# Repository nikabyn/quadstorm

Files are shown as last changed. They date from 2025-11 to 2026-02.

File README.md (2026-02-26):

# Project quadstorm (C010 Principles of Mobile Robotics)

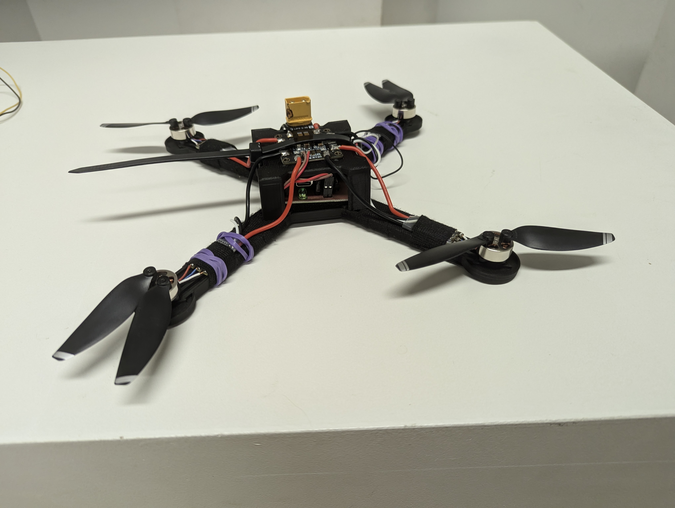
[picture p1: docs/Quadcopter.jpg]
Hier könnte ihre Werbung stehen


## Architecture
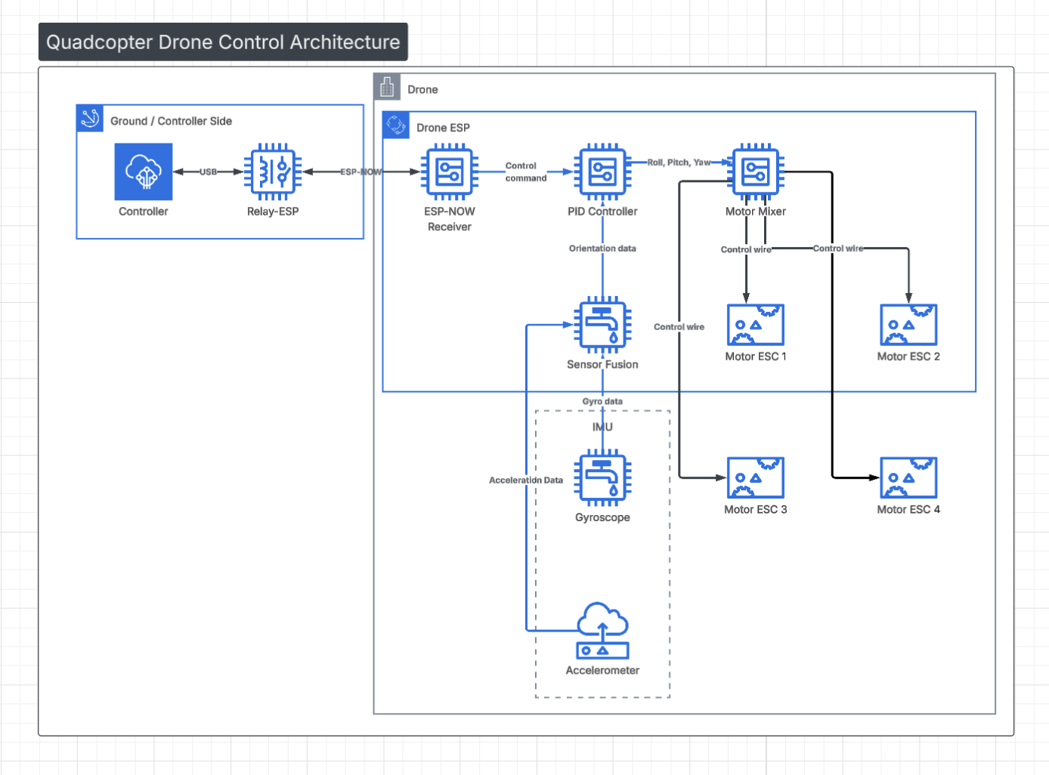
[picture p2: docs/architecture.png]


## Mainboard

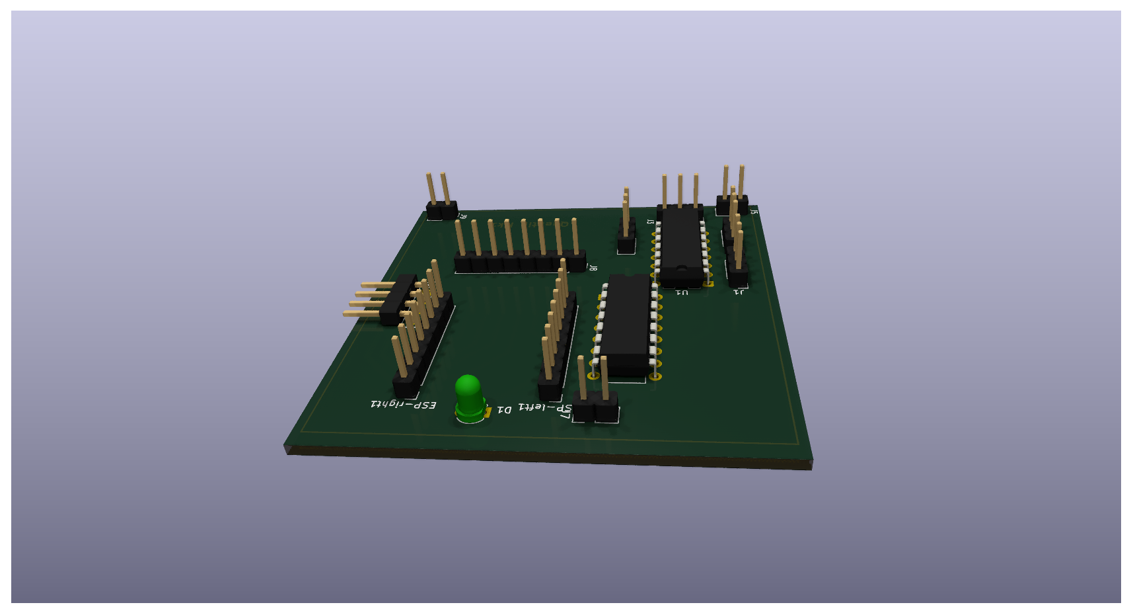
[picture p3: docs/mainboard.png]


## Parts-List:
- [BT2.0 550mAh 1S Battery](https://betafpv.com/products/bt2-0-550mah-1s-battery-4pcs#:~:text=Weight:%2013.99g/pc,VS%20450mAh%20Battery)
- IMU [BMI323](https://www.bosch-sensortec.com/products/motion-sensors/imus/bmi323/)
- Motors: [4x 2S Bldc 1503](https://www.amazon.de/dp/B0CK2KT3R3)
- ESP32-C6 ([ESP32-C6 Supermini](https://wiki.raudys.com/doku.php?id=esp32:esp32-c6_super_mini_board) / [DFR1117](https://wiki.dfrobot.com/SKU_DFR1117_Beetle_ESP32_C6))
- 74LS04 (Hex-Inverter), 74LS138 3-to-8 demux)
- [FVT LittleBee ESC 20A 2-4S](https://de.aliexpress.com/item/1005010298051292.html)
- Generic DJI compatible props
- 3d Printed Frame
- Custom Mainboard (manufactured via CNC Router)
- 12 M2x8 Screws

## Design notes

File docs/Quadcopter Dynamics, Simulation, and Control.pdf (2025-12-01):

## Quadcopter Dynamics, Simulation, and Control

## Introduction

A helicopter is a flying vehicle which uses rapidly spinning rotors to push air downwards, thus creating a thrust force keeping the helicopter aloft. Conventional helicopters have two rotors. These can be arranged as two coplanar rotors both providing upwards thrust, but spinning in opposite directions (in order to balance the torques exerted upon the body of the helicopter). The two rotors can also be arranged with one main rotor providing thrust and a smaller side rotor oriented laterally and counteracting the torque produced by the main rotor. However, these configurations require complicated machinery to control the direction of motion; a swashplate is used to change the angle of attack on the main rotors. In order to produce a torque the angle of attack is modulated by the location of each rotor in each stroke, such that more thrust is produced on one side of the rotor plane than the other. The complicated design of the rotor and swashplate mechanism presents some problems, increasing construction costs and design complexity.
A quadrotor helicopter (quadcopter) is a helicopter which has four equally spaced rotors, usually arranged at the corners of a square body. With four independent rotors, the need for a swashplate mechanism is alleviated. The swashplate mechanism was needed to allow the helicopter to utilize more degrees of freedom, but the same level of control can be obtained by adding two more rotors.
The development of quadcopters has stalled until very recently, because controlling four independent rotors has proven to be incredibly difficult and impossible without electronic assistance. The decreasing cost of modern microprocessors has made electronic and even completely autonomous control of quadcopters feasible for commercial, military, and even hobbyist purposes.
Quadcopter control is a fundamentally difficult and interesting problem. With six degrees of freedom (three translational and three rotational) and only four independent inputs (rotor speeds), quadcopters are severely underactuated. In order to achieve six degrees of freedom, rotational and translational motion are coupled. The resulting dynamics are highly nonlinear, especially after accounting for the complicated aerodynamic effects. Finally, unlike ground vehicles, helicopters have very little friction to prevent their motion, so they must provide their own damping in order to stop moving and remain stable. Together, these factors create a very interesting control problem. We will present a very simplified model of quadcopter dynamics and design controllers for our dynamics to follow a designated trajectory. We will then test our controllers with a numerical simulation of a quadcopter in flight.

## Quadcopter Dynamics

We will start deriving quadcopter dynamics by introducing the two frames in which will operate. The inertial frame is defined by the ground, with gravity pointing in the negative z direction. The body frame is defined by the orientation of the quadcopter, with the rotor axes pointing in the positive z direction and the arms pointing in the x and y directions.

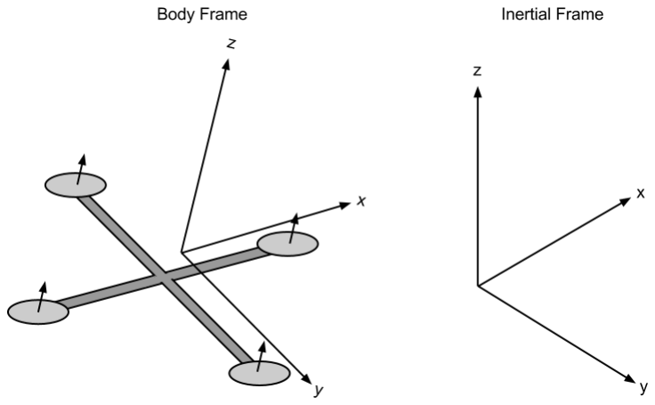
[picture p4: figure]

Quadcopter Body Frame and Inertial Frame

Kinematics

Before delving into the physics of quadcopter motion, let us formalize the kinematics in the body and inertial frames. We define the position and velocity of the quadcopter in the inertial frame as x = (x, y, z)

T and x˙ = (x˙, y˙, z˙)

T
, respectively. Similarly, we define the roll, pitch, and yaw angles in the body frame as θ = (φ, θ, ψ)

T
, with corresponding angular velocities equal to ˙θ = (φ˙,

˙θ, ψ˙)
T

. However, note that the angular velocity vector ω 6= ˙θ. The angular velocity is a vector pointing along the axis of rotation, while ˙θ is just the time derivative of yaw, pitch, and roll. In order to convert these angular velocities into the angular velocity vector, we can use the following relation:

ω =

1 | 0 | −sθ
0 | cφ | cθ

sφ
0 −sφ cθ cφ
- ˙θ

where ω is the angular velocity vector in the body frame.
We can relate the body and inertial frame by a rotation matrix R which goes from the body frame to the inertial frame. This matrix is derived by using the ZYZ Euler angle conventions and successively “undoing” the yaw, pitch, and roll.

R =

cφcψ − cθ

sφsψ | −cψsφ − cφcθ
sψ | sθ

sψ
cθ cψsφ + cφsψ | cφcθ cψ − sφsψ | −cψsθ
sφsθ | cφsθ | cθ

For a given vector ~v in the body frame, the corresponding vector is given by R~v in the inertial frame.

Physics

In order to properly model the dynamics of the system, we need an understanding of the physical properties that govern it. We will begin with a description of the motors being used for our quadcopter, and then use energy considerations to derive the forces and thrusts that these motors produce on the entire quadcopter. All motors on the quadcopter are identical, so we can analyze a single one without loss of generality. Note that adjacent propellers, however, are oriented opposite each other; if a propeller is spinning “clockwise”, then the two adjacent ones will be spinning “counter-clockwise”, so that torques are balanced if all propellers are spinning at the same rate.

Motors

Brushless motors are used for all quadcopter applications. For our electric motors, the torque produced is given by
τ = Kt(I − I0)

where τ is the motor torque, I is the input current, I0 is the current when there is no load on the motor, and Kt

is the torque proportionality constant. The voltage across the motor is the sum of the back-EMF and some resistive loss:

V = IRm + Kvω

where V is the voltage drop across the motor, Rm is the motor resistance, ω is the angular velocity of the motor, and Kv is a proportionality constant (indicating back-EMF generated per RPM). We can use this description of our motor to calculate the power it consumes. The power is

P = IV =

(τ + KtI0)(KtI0Rm + τRm + KtKvω)
Kt

2

For the purposes of our simple model, we will assume a negligible motor resistance. Then, the power becomes proportional to the angular velocity:

P ≈

(τ + KtI0)Kvω
Kt

Further simplifying our model, we assume that KtI0 τ. This is not altogether unreasonable, since I0 is the current when there is no load, and is thus rather small. In practice, this approximation holds well enough. Thus, we obtain our final, simplified equation for power:

P ≈

Kv
Kt

τω.

Forces

The power is used to keep the quadcopter aloft. By conservation of energy, we know that the energy the motor expends in a given time period is equal to the force generated on the propeller times the distance that the air it displaces moves (P · d t = F · d x). Equivalently, the power is equal to the thrust times the air velocity (P = F

d x
d t

).

P = Tvh

We assume vehicle speeds are low, so vh

is the air velocity when hovering. We also assume that the free stream velocity, v∞, is zero (the air in the surrounding environment is stationary relative to the quadcopter). Momentum theory gives us the equation for hover velocity as a function of thrust,

vh =

s
T
2ρA

where ρ is the density of the surrounding air and A is the area swept out by the rotor. Using our simplified equation for power, we can then write

P =

Kv
Kt

τω =

KvKτ
Kt

Tω =

T

3
2
p
2ρA

Note that in the general case, τ =~r × ~F; in this case, the torque is proportional to the thrust T by some constant ratio Kτ determined by the blade configuration and parameters. Solving for the thrust magnitude T, we obtain that thrust is proportional to the square of angular velocity of the motor:

T =

KvKτ

p
2ρA
Kt

ω

!2
= kω

2

where k is some appropriately dimensioned constant. Summing over all the motors, we find that the total thrust on the quadcopter (in the body frame) is given by

TB =

4
∑

i=1

Ti = k

0
0
∑ ωi

2

In addition to the thrust force, we will model friction as a force proportional to the linear velocity in each direction. This is a highly simplified view of fluid friction, but will be sufficient for our modeling and simulation. Our global drag forces will be modeled by an additional force term

FD =

−kdx˙
−kdy˙
−kdz˙

If additional precision is desired, the constant kd can be separated into three separate friction constants, one for each direction of motion. If we were to do this, we would want to model friction in the body frame rather than the inertial frame.

Torques

Now that we have computed the forces on the quadcopter, we would also like to compute the torques. Each rotor contributes some torque about the body z axis. This torque is the torque required to keep the propeller spinning and providing thrust; it creates the instantaneous angular acceleration and overcomes the frictional drag forces. The drag equation from fluid dynamics gives us the frictional force:

FD =

1
2

ρCD Av²

where ρ is the surrounding fluid density, A is the reference area (propeller cross-section, not area swept out by the propeller), and CD is a dimensionless constant. This, while only accurate in some in some cases, is good enough for our purposes. This implies that the torque due to drag is given by

τD =

1
2

RρCD Av² =

1
2

RρCD A(ωR)

2 = bω

2

where ω is the angular velocity of the propeller, R is the radius of the propeller, and b is some appropriately dimensioned constant. Note that we’ve assumed that all the force is applied at the tip of the propeller, which is certainly inaccurate; however, the only result that matters for our purposes is that the drag torque is proportional to the square of the angular velocity. We can then write the complete torque about the z axis for the ith motor:

τz = bω

2 + IMω˙

where IM is the moment of inertia about the motor z axis, ω˙ is the angular acceleration of the propeller, and b is our drag coefficient. Note that in steady state flight (i.e. not takeoff or landing), ω˙ ≈ 0, since most of the time the propellers will be maintaining a constant (or almost constant) thrust and won’t be accelerating. Thus, we ignore this term, simplifying the entire expression to
τz = (−1)

i+1
bωi

2
where the (−1)

i+1
term is positive for the ith propeller if the propeller is spinning clockwise and negative if it is spinning counterclockwise. The total torque about the z axis is given by the sum of all the torques from each propeller:

τψ = b

ω1

2 − ω2

2 + ω3

2 − ω4

2

The roll and pitch torques are derived from standard mechanics. We can arbitrarily choose the i = 1 and i = 3 motors to be on the roll axis, so

τφ = ∑r × T = L(kω1
2 − kω3
) = Lk(ω1

2 − ω3
)

Correspondingly, the pitch torque is given by a similar expression

τθ = Lk(ω2

2 − ω4

2
)

where L is the distance from the center of the quadcopter to any of the propellers. All together, we find that the torques in the body frame are

τB =

Lk(ω1

2 − ω3
2
)
Lk(ω2

2 − ω4

2
)
b
ω1

2 − ω2
2 + ω3
2 − ω4

2

The model we’ve derived so far is highly simplified. We ignore a multitude of advanced effects that contribute to the highly nonlinear dynamics of a quadcopter. We ignore rotational drag forces (our rotational velocities are relatively low), blade flapping (deformation of propeller blades due to high velocities and flexible materials), surrounding fluid velocities (wind), etc. With that said, we now have all the parts necessary to write out the dynamics of our quadcopter.

Equations of Motion

In the inertial frame, the acceleration of the quadcopter is due to thrust, gravity, and linear friction. We can obtain the thrust vector in the inertial frame by using our rotation matrix R to map the thrust vector from the body frame to the inertial frame. Thus, the linear motion can be summarized as

mx¨ =

0
0
−mg
- + RTB + FD

where ~x is the position of the quadcopter, g is the acceleration due to gravity, FD is the drag force, and TB is the thrust vector in the body frame.
While it is convenient to have the linear equations of motion in the inertial frame, the rotational equations of motion are useful to us in the body frame, so that we can express rotations about the center of the quadcopter instead of about our inertial center. We derive the rotational equations of motion from Euler’s equations for rigid body dynamics. Expressed in vector form, Euler’s equations are written as

Iω˙ + ω × (Iω) = τ

where ω is the angular velocity vector, I is the inertia matrix, and τ is a vector of external torques. We can rewrite this as

ω˙ =

ω˙ x
ω˙ y
ω˙ z
- = I

−1
(τ − ω × (Iω)).

We can model our quadcopter as two thin uniform rods crossed at the origin with a point mass (motor) at the end of each. With this in mind, it’s clear that the symmetries result in a diagonal inertia matrix of the form

I =

Ixx | 0 | 0
0 | Iyy | 0
0 | 0 | Izz

Therefore, we obtain our final result for the body frame rotational equations of motion

ω˙ =

τφ Ixx

−1

τθ

Iyy

−1

τψIzz

−1

- −

Iyy−Izz
Ixx

ωyωz
Izz−Ixx
Iyy

ωxωz
Ixx−Iyy
Izz

ωxωy

## Simulation

Now that we have complete equations of motion describing the dynamics of the system, we can create a simulation environment in which to test and view the results of various inputs and controllers. Although more advanced methods are available, we can quickly write a simulator which utilizes Euler’s method for solving differential equations to evolve the system state. In MATLAB, this simulator would be written as follows.

1 | % Simulation times, in seconds.
2 | start_time = 0;
3 | end_time = 10;
4 | dt = 0.005;
5 | times = start_time:dt:end_time;

6
7 | % Number of points in the simulation.
8 | N = numel(times);

9
10 | % Initial simulation state.
11 | x = [0; 0; 10];
12 | xdot = zeros(3, 1);
13 | theta = zeros(3, 1);

14
15 | % Simulate some disturbance in the angular velocity.
16 | % The magnitude of the deviation is in radians / second.
17 | deviation = 100;
18 | thetadot = deg2rad(2 * deviation * rand(3, 1) - deviation);

19
20 | % Step through the simulation, updating the state.
21 | for t = times
22 | % Take input from our controller.
23 | i = input(t);

24
25 | omega = thetadot2omega(thetadot, theta);

26
27 | % Compute linear and angular accelerations.
28 | a = acceleration(i, theta, xdot, m, g, k, kd);
29 | omegadot = angular_acceleration(i, omega, I, L, b, k);

30
31 | omega = omega + dt * omegadot;
32 | thetadot = omega2thetadot(omega, theta);
33 | theta = theta + dt * thetadot;
34 | xdot = xdot + dt * a;
35 | x = x + dt * xdot;
36 | end

We would then need functions to compute all of the physical forces and torques.

1 | % Compute thrust given current inputs and thrust coefficient.
2 | function T = thrust(inputs, k)
3 | % Inputs are values for ωi
| 2
4 | T = [0; 0; k * sum(inputs)];
5 | end

6
7 | % Compute torques, given current inputs, length, drag coefficient, and thrust coefficient.
8 | function tau = torques(inputs, L, b, k)
9 | % Inputs are values for ωi
| 2
10 | tau = [
11 | L * k * (inputs(1) - inputs(3))

L * k * (inputs(2) - inputs(4))
b * (inputs(1) - inputs(2) + inputs(3) - inputs(4))

];
end

function a = acceleration(inputs, angles, xdot, m, g, k, kd) gravity = [0; 0; -g];
R = rotation(angles);
T = R * thrust(inputs, k);
Fd = -kd * xdot;
a = gravity + 1 / m * T + Fd;
end

function omegadot = angular_acceleration(inputs, omega, I, L, b, k) tau = torques(inputs, L, b, k);
omegaddot = inv(I) * (tau - cross(omega, I * omega));
end

We would also need values for all of our physical constants, a function to compute the rotation matrix R, and functions to convert from an angular velocity vector ω to the derivatives of roll, pitch, and yaw and vice-versa. These are not shown. We can then draw the quadcopter in a three-dimensional visualization which is updated as the simulation is running.

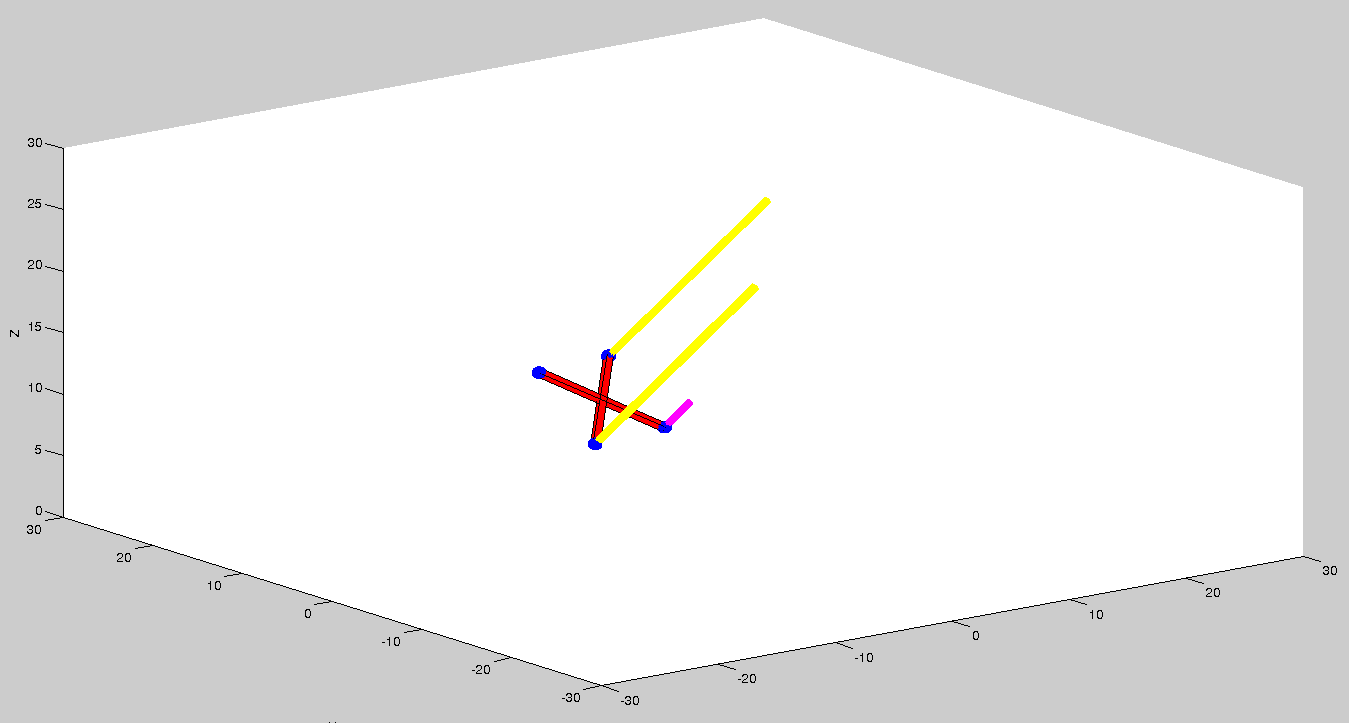
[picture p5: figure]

Quadcopter Simulation. Bars above each propeller represent, roughly, relative thrust magnitudes.

## Control

The purpose of deriving a mathematical model of a quadcopter is to assist in developing controllers for physical quadcopters. The inputs to our system consist of the angular velocities of each rotor, since all we can control is the voltages across the motors. Note that in our simplified model, we only use the square of the angular velocities, ωi

2
, and never the angular
velocity itself, ωi
. For notational simplicity, let us introduce the inputs γi = ωi

2
. Since we
can set ωi

, we can clearly set γi as well. With this, we can write our system as a first order differential equation in state space. Let x1 be the position in space of the quadcopter, x2 be the quadcopter linear velocity, x3 be the roll, pitch, and yaw angles, and x4 be the angular velocity vector. (Note that all of these are 3-vectors.) With these being our state, we can write the state space equations for the evolution of our state.

x˙1 = x2

x˙2 =

0
0
−g
- +

1
m

RTB +

1
m

FD

x˙3 =

1 | 0 | −sθ
0 | cφ | cθ sφ
0 −sφ | cθ cφ

−1
x4

x˙4 =

τφ Ixx

−1

τθ

Iyy

−1

τψIzz

−1

- −

Iyy−Izz
Ixx

ωyωz
Izz−Ixx
Iyy

ωxωz
Ixx−Iyy
Izz

ωxωy

Note that our inputs are not used in these equations directly. However, as we will see, we can choose values for τ and T, and then solve for values of γi

PD Control

In order to control the quadcopter, we will use a PD control, with a component proportional to the error between our desired trajectory and the observed trajectory, and a component proportional to the derivative of the error. Our quadcopter will only have a gyro, so we will only be able to use the angle derivatives φ˙,

˙θ, and ψ˙ in our controller; these measured values will give us the derivative of our error, and their integral will provide us with the actual error. We would like to stabilize the helicopter in a horizontal position, so our desired velocities and angles will all be zero. Torques are related to our angular velocities by τ = I

¨θ, so we would
like to set the torques proportional to the output of our controller, with τ = Iu(t). Thus,

τφ
τθ
τψ
- =

−Ixx
Kdφ˙ + Kp

R T
0

φ˙d t

−Iyy
Kd

˙θ + Kp

R T
0

˙θd t

−Izz
Kdψ˙ + Kp

R T
0

ψ˙d t

We have previously derived the relationship between torque and our inputs, so we know that

τB =

Lk(γ1 − γ3)
Lk(γ2 − γ4)
b (γ1 − γ2 + γ3 − γ4)
- =

−Ixx
Kdφ˙ + Kp

R T
0

φ˙d t

−Iyy
Kd

˙θ + Kp

R T
0

˙θd t

−Izz
Kdψ˙ + Kp

R T
0

ψ˙d t

This gives us a set of three equations with four unknowns. We can constrain this by enforcing the constraint that our inputs must keep the quadcopter aloft:

T = mg.

Note that this equation ignores the fact that the thrust will not be pointed directly up. This will limit the applicability of our controller, but should not cause major problems for small deviations from stability. If we had a way of determining the current angle accurately, we could compensate. If our gyro is precise enough, we can integrate the values obtained from the gyro to get the angles θ and φ. In this case, we can calculate the thrust necessary to keep the quadcopter aloft by projecting the thrust mg onto the inertial z axis. We find that

Tproj = mg cos θ cos φ

Therefore, with a precise angle measurement, we can instead enforce the requirement that the thrust be equal to
T =

mg
cos θ cos φ in which case the component of the thrust pointing along the positive z axis will be equal to mg. We know that the thrust is proportional to a weighted sum of the inputs:

T =

mg
cos θ cos φ

= k∑γi =⇒ ∑γi =

mg
k cos θ cos φ

With this extra constraint, we have a set of four linear equations with four unknowns γi . We
can then solve for each γi

, and obtain the following input values:

γ1 =

mg
4k cos θ cos φ

−

2beφ Ixx + eψIzzkL
4bkL

γ2 =

mg
4k cos θ cos φ

+

eψIzz
4b

−

eθ

Iyy
2kL

γ3 =

mg
4k cos θ cos φ

−

−2beφ Ixx + eψIzzkL
4bkL

γ4 =

mg
4k cos θ cos φ

+

eψIzz
4b

+

eθ

Iyy
2kL

This is a complete specification for our PD controller. We can simulate this controller using our simulation environment. The controller drives the angular velocities and angles to zero.

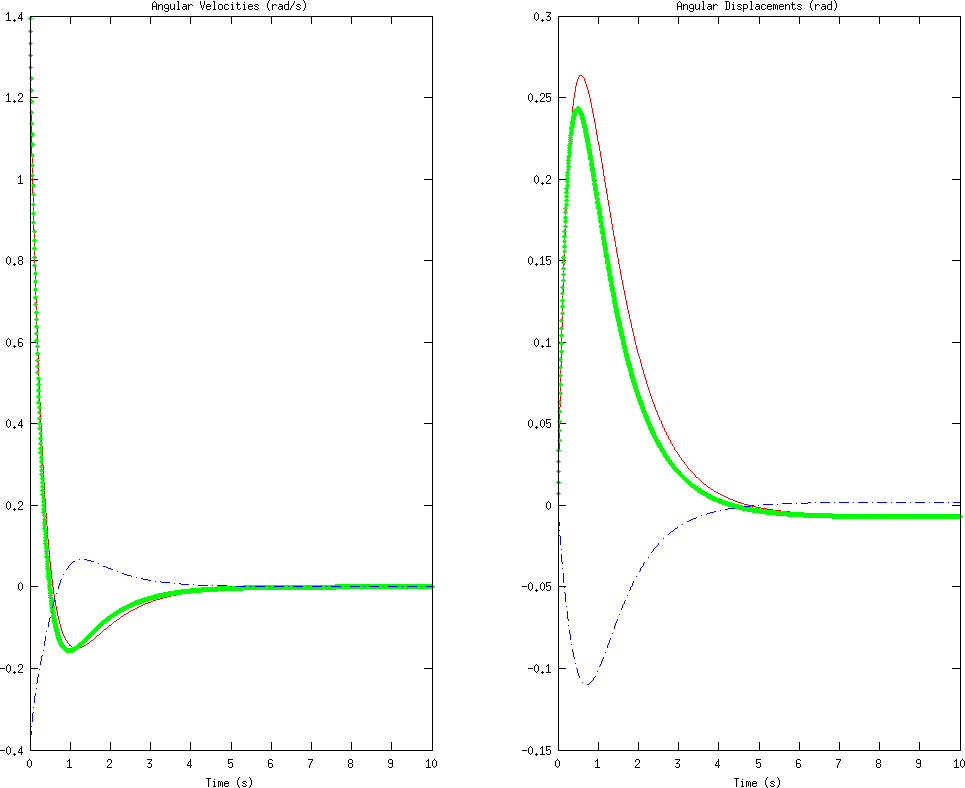
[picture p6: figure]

Left: Angular velocities. Right: angular displacements. φ, θ, ψ are coded as red, green, and blue.

However, note that the angles are not completely driven to zero. The average steady state error (error after 10 seconds of simulation) is approximately 0.3◦
. This is a common problem with using PD controllers for mechanical systems, and can be partially alleviated with a PID controller, as we will discuss in the next section.
In addition, note that since we are only controlling angular velocities, our positions and linear velocities do not converge to zero. However, the z position will remain constant, because we have constrained the total vertical thrust to be such that it keeps the quadcopter perfectly aloft, without ascending or descending. However, this is really nothing more than a curiosity. With the limited sensing that we have available to us, there is nothing we can do to control the linear position and velocity of the quadcopter. While in theory we could compute the linear velocities and positions from the angular velocities, in practice the values will be so noisy as to be completely useless. Thus, we will restrict ourselves to just stabilizing the quadcopter angle and angular velocity. (Traditionally, navigation is done by a human, and stabilization is there simply to make control easier for the human operator.)

We have implemented this PD control for use in our simulation. The controller is implemented as a function which is given some state (corresponding to controller state, not system state) and the sensor inputs, and must compute the inputs γi and the updated state. The code for a PD control follows.

% Compute system inputs and updated state.
% Note that input = [γ1, . . ., γ4]
function [input, state] = pd_controller(state, thetadot) % Controller gains, tuned by hand and intuition.
Kd = 4;
Kp = 3;

% Initialize the integral if necessary. if ˜isfield(state, ’integral’) params.integral = zeros(3, 1);
end

% Compute total thrust
total = state.m * state.g / state.k / (cos(state.integral(1)) * cos(state.integral(2)));

% Compute errors
e = Kd * thetadot + Kp * params.integral;

% Solve for the inputs, γi
input = error2inputs(params, accels, total);

% Update the state
params.integral = params.integral + params.dt .* thetadot; end

PID Control

PD controllers are nice in their simplicity and ease of implementation, but they are often inadequate for controlling mechanical systems. Especially in the presence of noise and disturbances, PD controllers will often lead to steady state error. A PID control is a PD control with another term added, which is proportional to the integral of the process variable. Adding an integral term causes any remaining steady-state error to build up and enact a change, so a PID controller should be able to track our trajectory (and stabilize the quadcopter) with a significantly smaller steady-state error. The equations remain identical to the ones presented in the PD case, but with an additional term in the error:

eφ = Kdφ˙ + Kp

Z T

0

φ˙d t + Ki

Z T

0

Z T

0

φ˙d td t

eθ = Kd

˙θ + Kp

Z T

0

˙θd t + Ki

Z T

0

Z T

0

˙θd td t

eψ = Kdψ˙ + Kp

Z T

0

ψ˙d t + Ki

Z T

0

Z T

0

ψ˙d td t

However, PID controls come with their own shortcomings. One problem that commonly occurs with a PID control is known as integral windup.

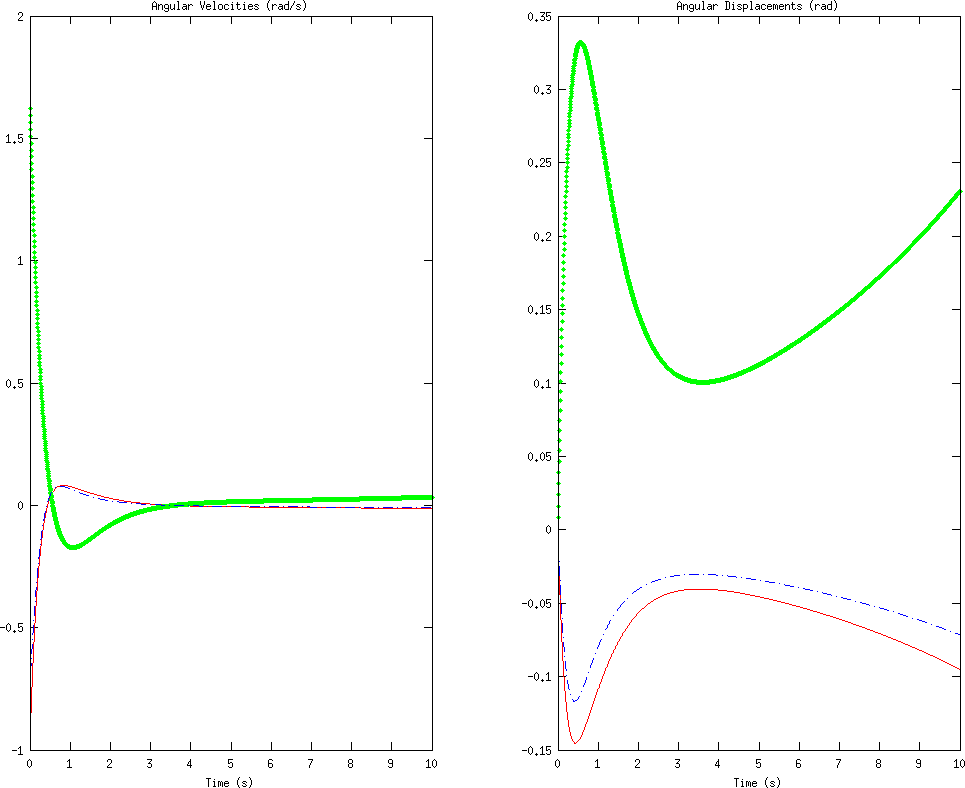
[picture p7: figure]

In some cases, integral wind-up can cause lengthy oscillations instead of settling. In other cases, wind-up may actually cause the system to become unstable, instead of taking longer to reach a steady state.

If there is a large disturbance in the process variable, this large disturbance is integrated over time, becoming a still larger control signal (due to the integral term). However, even once the system stabilizes, the integral is still large, thus causing the controller to overshoot its target. It may then begin a series of dieing down oscillations, become unstable, or simply take an incredibly long time to reach a steady state. In order to avoid this, we disable the integral function until we reach something close to the steady state. Once we are in a controllable region near the desired steady state, we turn on the integral function, which pushes the system towards a low steady-state error.

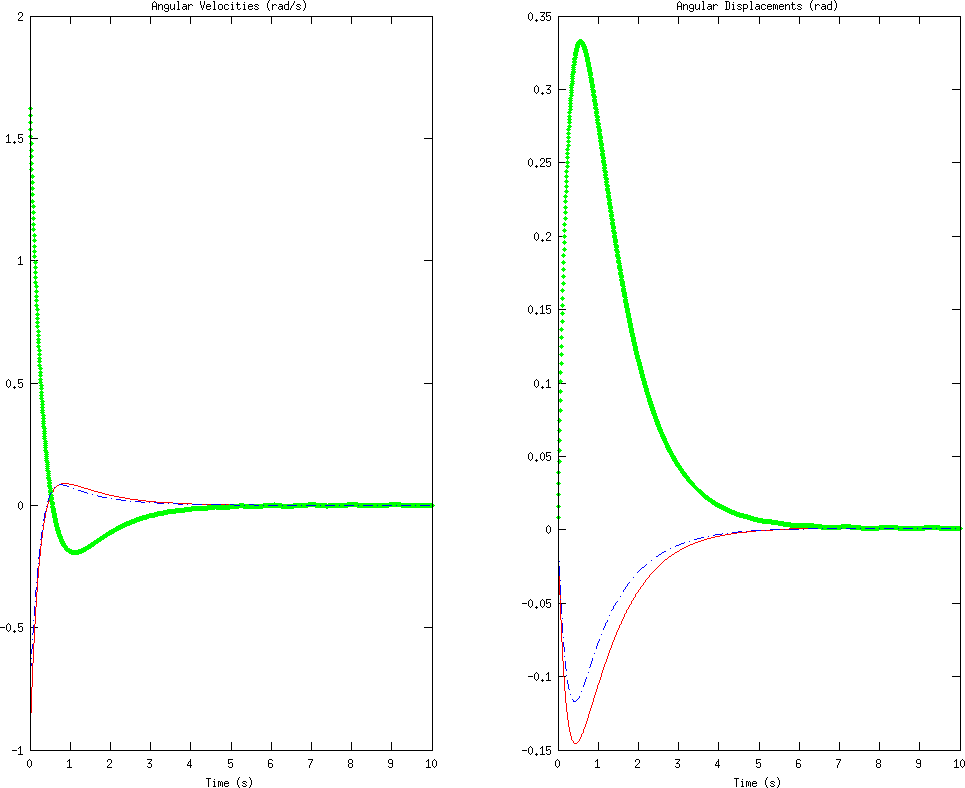
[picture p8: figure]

With a properly implemented PID, we achieve an error of approximately 0.06◦ after 10 seconds.
We have implemented this PID control for use in simulation, in the same way as with the PD controller shown earlier. Note that there is an additional parameter to tune in a PID. The disturbances used for all the test cases are identical, shown to compare the controllers.

% Compute system inputs and updated state.
% Note that input = [γ1, . . ., γ4]
function [input, state] = pid_controller(state, thetadot) % Controller gains, tuned by hand and intuition.
Kd = 4;
Kp = 3;
Ki = 5.5;

% Initialize the integral if necessary. if ˜isfield(state, ’integral’) params.integral = zeros(3, 1); params.integral2 = zeros(3, 1); end

% Prevent wind-up
if max(abs(params.integral2)) > 0.01 params.integral2(:) = 0;
end

% Compute total thrust
total = state.m * state.g / state.k / (cos(state.integral(1)) * cos(state.integral(2)));

% Compute errors

24 | e = Kd * thetadot + Kp * params.integral - Ki * params.integral2;
26 | % Solve for the inputs, γi
27 | input = error2inputs(params, accels, total);

28
29 | % Update the state
30 | params.integral = params.integral + params.dt .* thetadot;
31 | params.integral2 = params.integral2 + params.dt .* params.integral;
32 | end

Automatic PID Tuning

Although PID control has the potential to perform very well, it turns out that the quality of the controller is highly dependent on the gain parameters. Tuning the parameters by hand may be quite difficult, as the ratios of the parameters is as important as the magnitudes of the parameters themselves; often, tuning parameters requires detailed knowledge of the system and an understanding of the conditions in which the PID control will be used. The parameters we chose previously were tuned by hand for good performance, simply by running simulations with many possibly disturbances and parameter values, and choosing something that worked reasonably well. This method is clearly suboptimal, not only because it can be very difficult and labor-intensive (and sometimes more or less impossible) but also because the resulting gains are not in any way guaranteed to be optimal or even close to optimal.
Ideally, we would be able to use an algorithm to analyze a system and output the “optimal” PID gains, for some reasonable definition of optimal. This problem has been studied in depth, and many methods have been proposed. Many of these methods require detailed knowledge of the system being modeled, and some rely on properties of the system, such as stability or linearity. The method we will use for choosing our PID parameters is a method known as extremum seeking.
Extremum seeking works exactly as the name implies. We define the “optimal” set of parameters as some vector ~θ = (Kp, Ki
, Kd

) which minimizes some cost function J(~θ). In our case, we would like to define a cost function that penalizes high error and error over extended durations of time. One candidate cost function is given by

J(~θ) = 1 tf − to

# Z tf

t0

e(t,~θ)
2d t

where e(t,~θ) is the error in following some reference trajectory with some initial disturbance using a set of parameters ~θ. Suppose we were able to somehow compute the gradient of this cost function, ∇J(~θ). In that case, we could iteratively improve our parameter vector by defining a parameter update rule

~θ(k + 1) = ~θ(k) − α∇J(~θ)

where~θ(k) is the parameter vector after k iterations and α is some step size which dictates how much we adjust our parameter vector at each step of the iteration. As k → ∞, the cost function J(~θ) will approach a local minimum in the space of PID parameters.
The question remains as to how we can estimate ∇J(~θ). By definition,

∇J(~θ) =
∂ ∂Kp | J(~θ),

∂
∂Ki

J(~θ),

∂
∂Kd

J(~θ)

We know how to compute J(~θ). Using this, we can approximate the derivative with respect to any of the gains numerically, simply by computing

∂
∂K

J(~θ) ≈

J(~θ + δ · uˆK) − J(~θ − δ · uˆK) 2δ
where uˆK is the unit vector in the K direction. As δ → 0, this approximation becomes better. Using this approximation, we can minimize our cost function and achieve locally optimal PID parameters. We can start with randomly initialized positive weights, disturb the system in some set manner, evaluate J(~θ) by simulating the system for different PID parameters, and then compute the gradient. Then, using the method of gradient descent, we can iteratively oprtimize our gains until we have some form of convergence.
The gradient descent method does, however, have several problems. First of all, although it finds a local minimum, that minimum is only guaranteed to be a local minimum
- there may be other minima which are better global minima. In order to avoid choosing suboptimal local minima in the cost function, we repeat our optimization several times, and choose the best result. We initialize our PID parameters randomly, so each time we run the optimization we will get a different result. In addition, instead of choosing disturbance and then optimizing the response to that disturbance, we use several random disturbances at each iteration and use the average response to compute costs and gradients. This ensures that our parameters are general and not optimized for a specific disturbance. In addition, we vary the step size and the number of disturbances to try per iteration, in order to increase the sensitivity of our results as our iteration continues. We stop iterations when we detect a steady state, which we do by computing a linear regression on the most recent costs and iterating until the slope is statistically indistinguishable from zero using a 99% confidence interval.
Using our quadcopter simulation, we can define a function that computes the cost for a given set of PID parameters.
1 | function J = cost(theta)
2 | % Create a controller using the given gains.
3 | control = controller(’pid’, theta(1), theta(2), theta(3));

4
5 | % Perform a simulation.
6 | data = simulate(control);

7
8 | % Compute the integral, | 1
| | tf − t0

### R tf

t0

e(t)

2 dt

9 | t0 = 0;
10 | tf = 1;
11 | J = 1/(tf - t0) * sum(data.theta(data.t >= t0 & data.t <= tf) .ˆ 2) * data.dt;
12 | end

We can use this function to approximate a derivative with respect to a gain:

1 | % Compute derivative with respect to first parameter.
2 | delta = 0.01;
3 | var = [1, 0, 0];
4 | derivative = (cost(theta + delta * var) - cost(theta - delta * var)) / (2 * delta);

We can then use our gradient descent method (with all modifications described above) to
minimize the cost function and obtain a good set of PID parameters. We can verify that our
tuning method is working by visualizing the cost function versus the iteration number, and
seeing that the cost function is indeed going down and stabilizing at a local minimum.

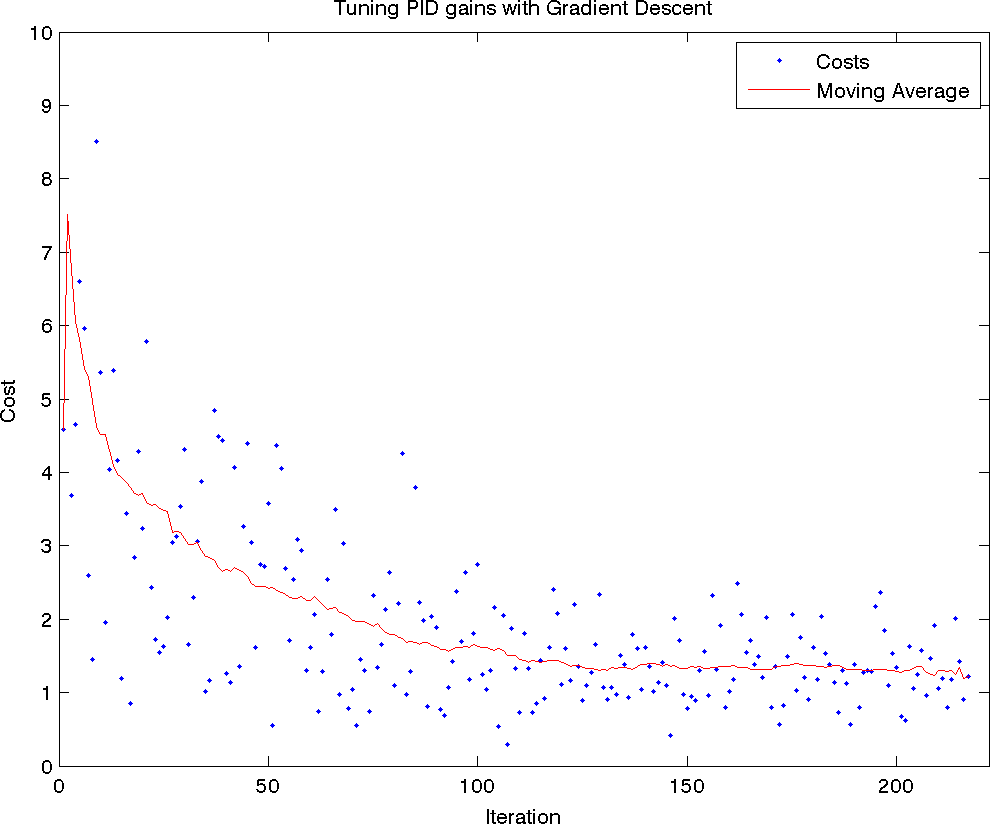
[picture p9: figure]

Cost function plotted as a function of iteration number, along with moving average. Tuning stops when the slope of the moving average becomes statistically indistinguishable from zero with a 99% confidence interval.

We can compare the manually-chosen PID parameters with those designed by the algorithm.

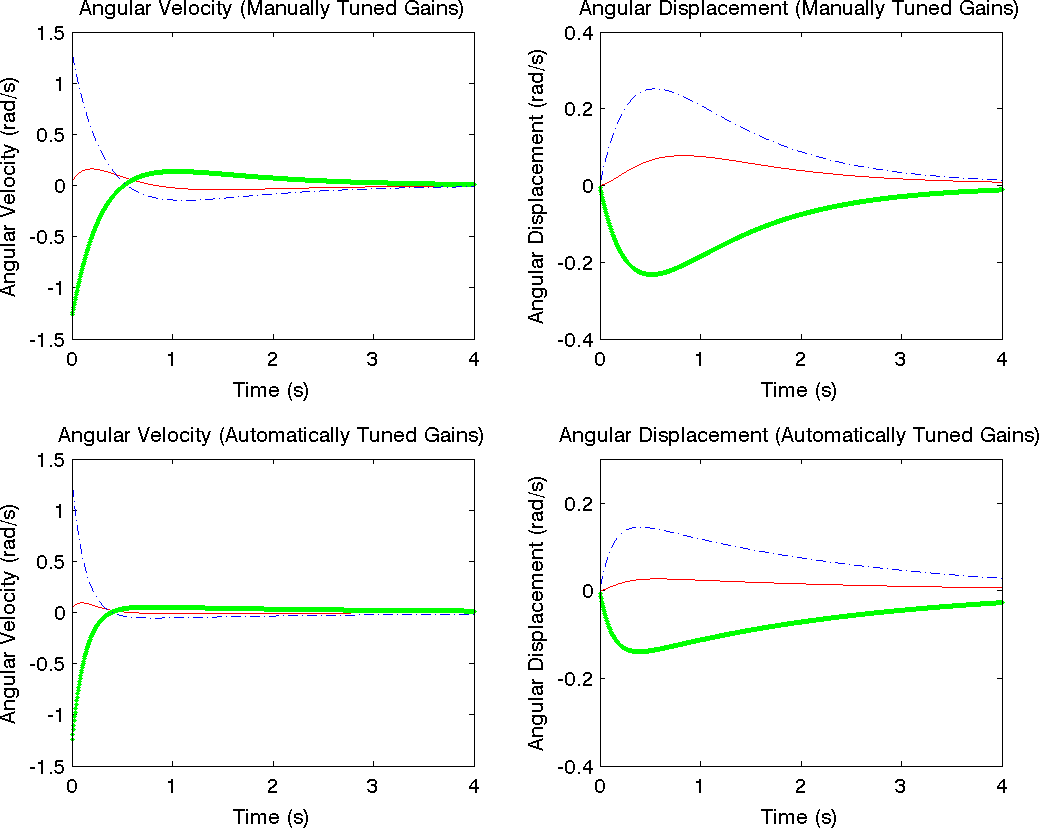
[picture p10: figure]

Top: Angular velocities and angular displacements, using manually tuned PID controller. Bottom: Angular velocities and angular displacements, using automatically tuned PID controller.

The automatically-chosen PID parameters do significantly better overall. They have significantly smaller swings in value, overshoot significantly less, and converge faster. However, the error in the angular displacement takes longer to converge to zero with the automatically tuned parameters than with the manually turned parameters, although the initial convergence is much better when the parameters are chosen via gradient descent. This is due to the fact that our cost function emphasizes squared error, and thus gives priority to minimizing overall error magnitude rather than long-term convergence. We could easily modify our cost function to give higher priority to long-term error, in which case the automatically-tuned parameters are likely to do better.

## Conclusion

We derived equations of motion for a quadcopter, starting with the voltage-torque relation for the brushless motors and working through the quadcopter kinematics and dynamics. We ignored aerodynamical effects such as blade-flapping and non-zero free stream velocity, but included air friction as a linear drag force in all directions. We used the equations of motion to create a simulator in which to test and visualize quadcopter control mechanisms.
We began with a simple PD controller. Although the PD controller worked, it left a significant steady-state error. In order to decrease the steady-state error, we added an integral term in order to create a PID controller. We tested the PID controller (with minor modifications to prevent integral wind-up) and found that it was better at preventing steady-state error than the PD controller when presented with the same disturbances and using the same proportional and derivative gains. We also found that tuning the PID controller was difficult, and would often lead to an unstable system for unknown reasons. In order to avoid the difficulty of PID tuning and find the optimal set of parameters, we used a gradient-descent based extremum seeking method in order to numerically estimate gradients of a cost function in PID-parameter space and iteratively choose a set of parameters to minimize the cost function. We found that the resulting controller was significantly better than the one using manually turned parameters.

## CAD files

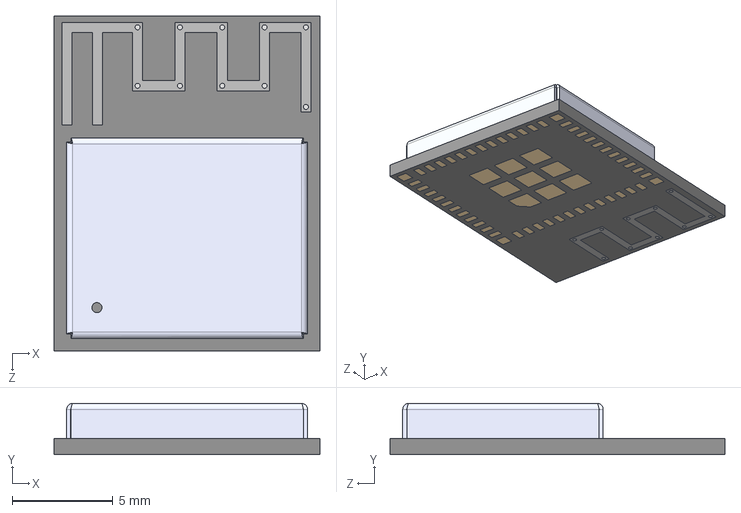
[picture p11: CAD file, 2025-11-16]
hardware/mainboard/Parts/ESP32-C6-MINI-4/ESP32-C6-MINI-1-N4.step
13.2 x 2.55 x 16.6 mm

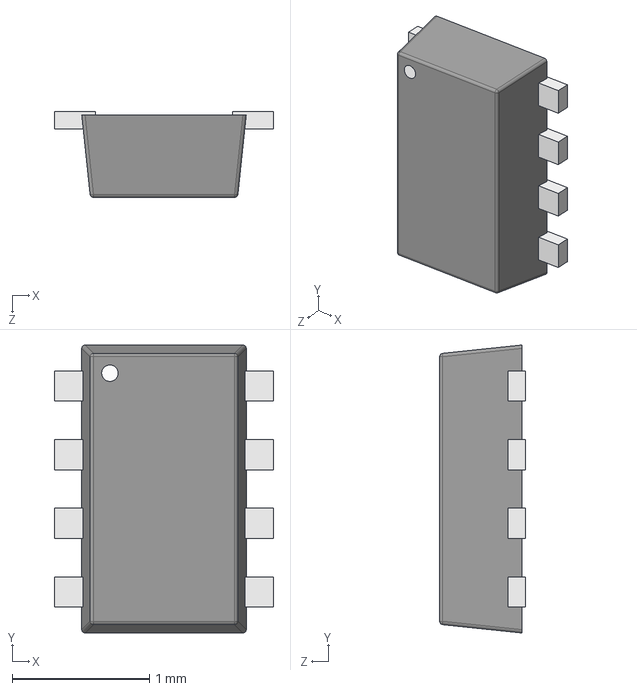
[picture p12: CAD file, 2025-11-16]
hardware/mainboard/Parts/MP2338GTL-Z/MP2338GTL-Z.stp
1.60 x 2.10 x 0.625 mm

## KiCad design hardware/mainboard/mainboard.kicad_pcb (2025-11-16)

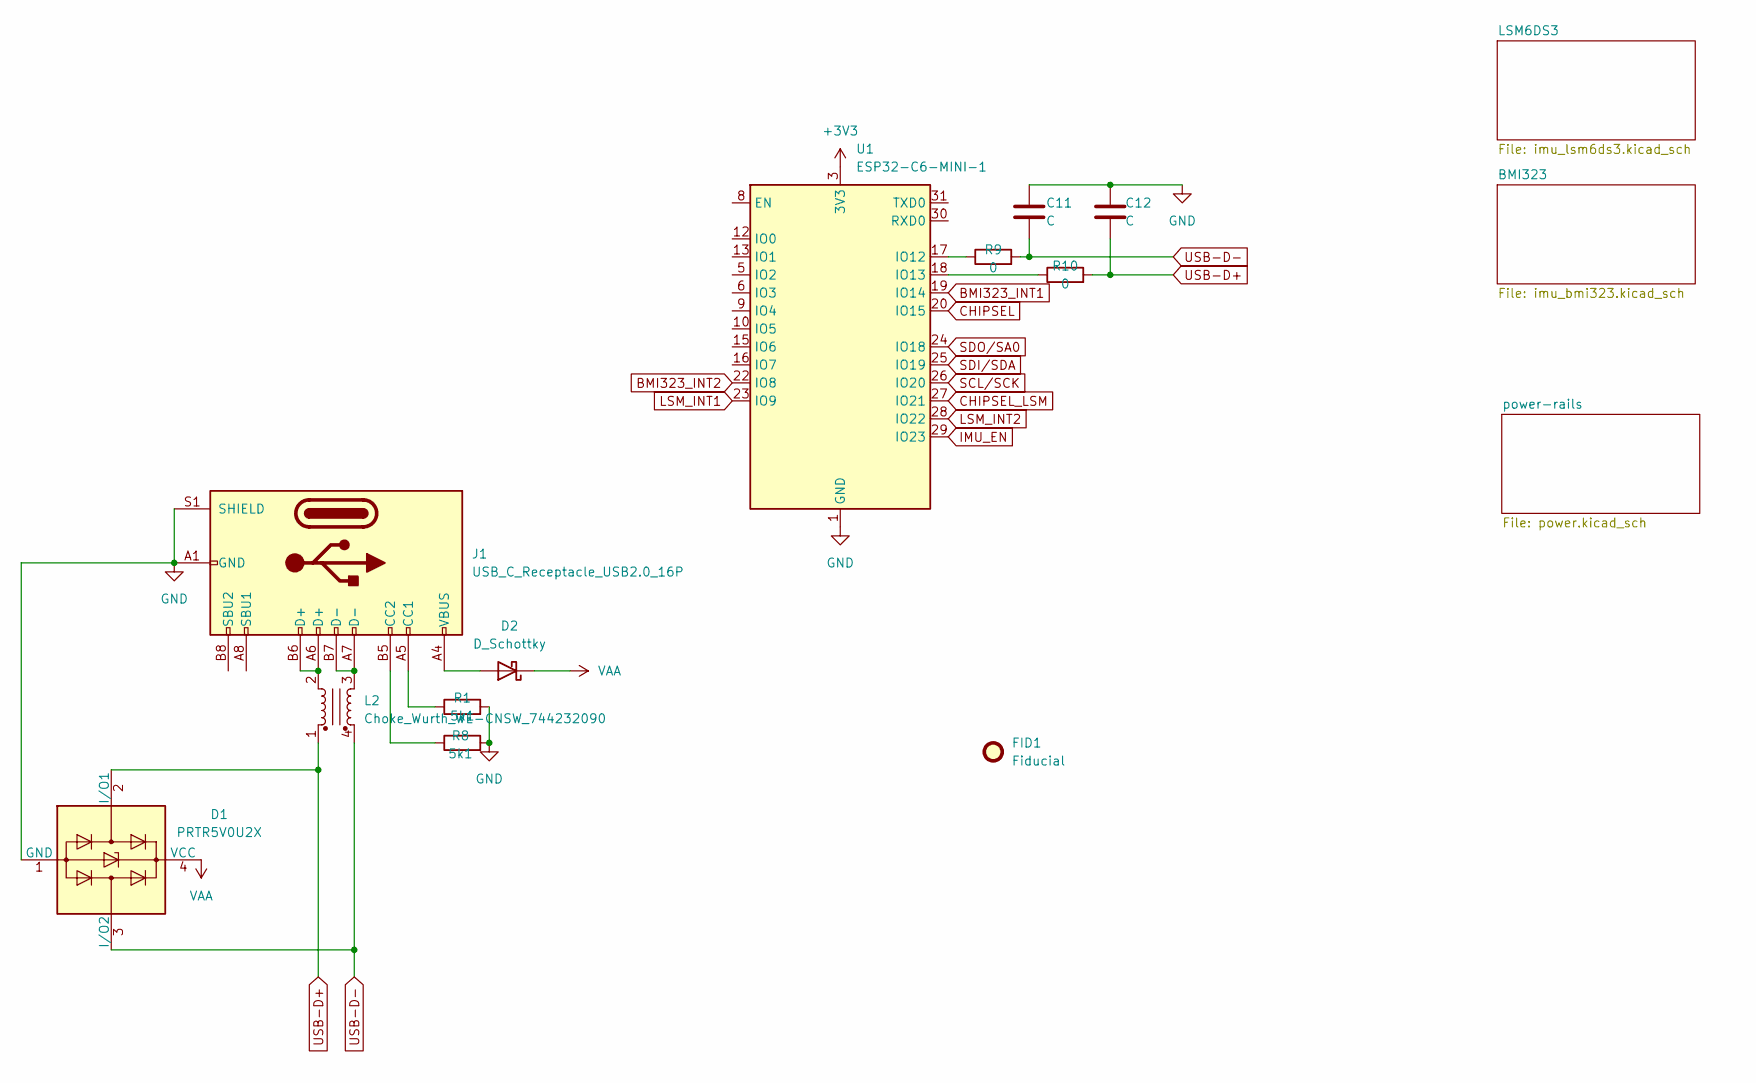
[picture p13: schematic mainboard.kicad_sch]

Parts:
C11, C12: C; C_0402_1005Metric
D1: PRTR5V0U2X; SOT-143
D2: D_Schottky; D_0805_2012Metric
FID1: Fiducial; Fiducial_0.5mm_Mask1.5mm
J1: USB_C_Receptacle_USB2.0_16P; USB_C_Receptacle_GCT_USB4105-xx-A_16P_TopMnt_Horizontal
L2: Choke_Wurth_WE-CNSW_744232090; L_CommonMode_Wurth_WE-CNSW-1206
R1, R8: 5k1; R_0603_1608Metric
R9, R10: 0; R_0603_1608Metric
U1: ESP32-C6-MINI-1

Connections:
+3V3: U1.3 (3V3); also elsewhere on the board
BMI323_INT1: U1.19 (IO14); also elsewhere on the board
BMI323_INT2: U1.22 (IO8); also elsewhere on the board
CHIPSEL: U1.20 (IO15); also elsewhere on the board
CHIPSEL_LSM: U1.27 (IO21); also elsewhere on the board
GND: C11.1, C12.1, D1.1 (GND), J1.A1 (GND), J1.A12 (GND), J1.B1 (GND), J1.B12 (GND), J1.S1 (SHIELD), R1.2, R8.2, U1.1 (GND), U1.2 (GND), U1.11 (GND), U1.14 (GND), U1.36 (GND), U1.37 (GND), U1.38 (GND), U1.39 (GND), U1.40 (GND), U1.41 (GND), U1.42 (GND), U1.43 (GND), U1.44 (GND), U1.45 (GND), U1.46 (GND), U1.47 (GND), U1.48 (GND), U1.49 (GND), U1.50 (GND), U1.51 (GND), U1.52 (GND), U1.53 (GND); also elsewhere on the board
IMU_EN: U1.29 (IO23); also elsewhere on the board
LSM_INT1: U1.23 (IO9); also elsewhere on the board
LSM_INT2: U1.28 (IO22); also elsewhere on the board
unnamed: D2.2 (A), J1.A4 (VBUS), J1.A9 (VBUS), J1.B4 (VBUS), J1.B9 (VBUS)
unnamed: J1.A5 (CC1), R1.1
unnamed: J1.B5 (CC2), R8.1
unnamed: J1.A6 (D+), J1.B6 (D+), L2.2
unnamed: J1.A7 (D-), J1.B7 (D-), L2.3
unnamed: R9.1, U1.17 (IO12)
unnamed: R10.1, U1.18 (IO13)
SCL/SCK: U1.26 (IO20); also elsewhere on the board
SDI/SDA: U1.25 (IO19); also elsewhere on the board
SDO/SA0: U1.24 (IO18); also elsewhere on the board
USB-D+: C12.2, D1.2 (I/O1), L2.1, R10.2
USB-D-: C11.2, D1.3 (I/O2), L2.4, R9.2
VAA: D1.4 (VCC), D2.1 (K); also elsewhere on the board

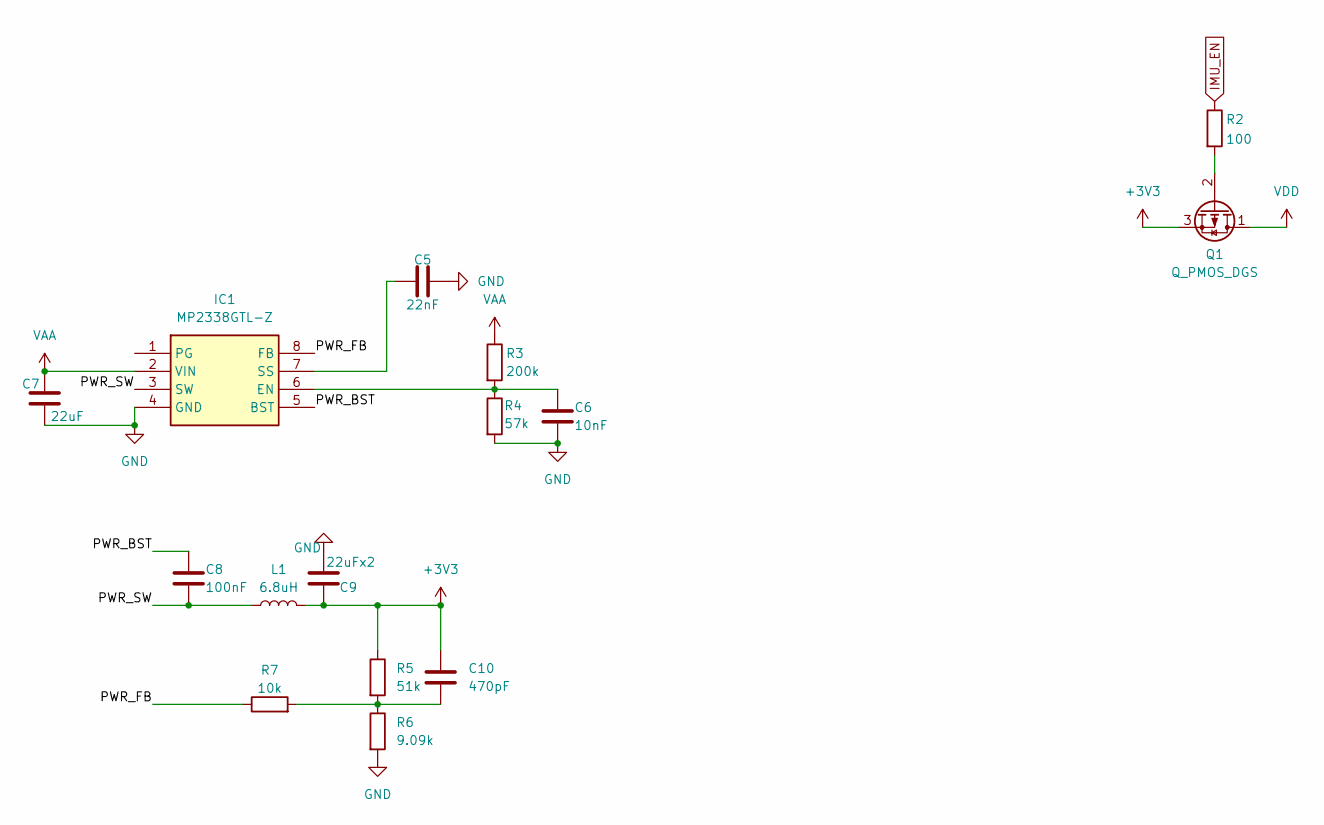
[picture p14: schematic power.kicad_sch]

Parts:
C5: 22nF; C_0402_1005Metric
C6: 10nF; C_0402_1005Metric
C7: 22uF; C_0402_1005Metric
C8: 100nF; C_0402_1005Metric
C9: 22uFx2; C_0402_1005Metric
C10: 470pF; C_0402_1005Metric
IC1: MP2338GTL-Z; MP2338GTLZ; Manufacturer_Part_Number MP2338GTL-Z; Mouser Part Number 946-MP2338GTL-Z
L1: 6.8uH; L_0805_2012Metric_Pad1.05x1.20mm_HandSolder
Q1: Q_PMOS_DGS; SOT-23-3
R2: 100; R_0603_1608Metric
R3: 200k; R_0603_1608Metric
R4: 57k; R_0603_1608Metric
R5: 51k; R_0603_1608Metric
R6: 9.09k; R_0603_1608Metric
R7: 10k; R_0603_1608Metric

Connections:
+3V3: C9.1, C10.1, L1.2, Q1.3 (S), R5.1; also elsewhere on the board
/power-rails/PWR_BST: C8.1, IC1.5 (BST)
/power-rails/PWR_FB: IC1.8 (FB), R7.1
/power-rails/PWR_SW: C8.2, IC1.3 (SW), L1.1
GND: C5.2, C6.2, C7.2, C9.2, IC1.4 (GND), R4.2, R6.2; also elsewhere on the board
IMU_EN: R2.1; also elsewhere on the board
unnamed: C10.2, R5.2, R6.1, R7.2
unnamed: C6.1, IC1.6 (EN), R3.2, R4.1
unnamed: C5.1, IC1.7 (SS)
unnamed: Q1.2 (G), R2.2
VAA: C7.1, IC1.2 (VIN), R3.1; also elsewhere on the board
VDD: Q1.1 (D); also elsewhere on the board

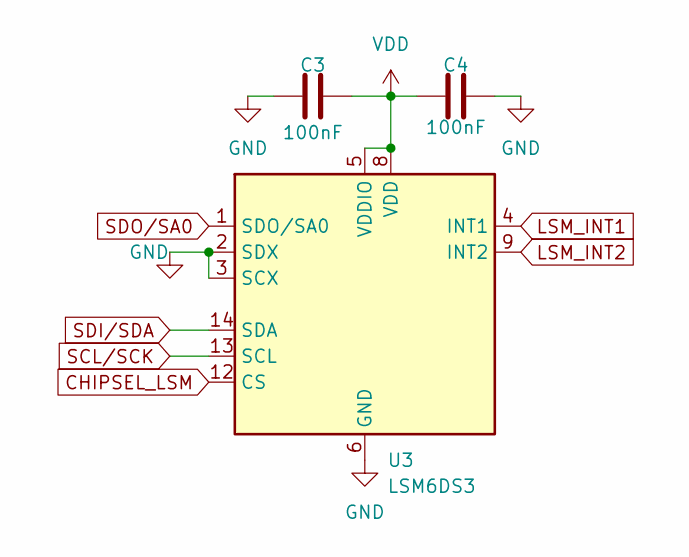
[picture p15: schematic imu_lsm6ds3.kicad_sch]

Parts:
C3, C4: 100nF; C_0402_1005Metric
U3: LSM6DS3; LGA-14_3x2.5mm_P0.5mm_LayoutBorder3x4y

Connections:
CHIPSEL_LSM: U3.12 (CS); also elsewhere on the board
GND: C3.1, C4.2, U3.2 (SDX), U3.3 (SCX), U3.6 (GND), U3.7 (GND); also elsewhere on the board
LSM_INT1: U3.4 (INT1); also elsewhere on the board
LSM_INT2: U3.9 (INT2); also elsewhere on the board
SCL/SCK: U3.13 (SCL); also elsewhere on the board
SDI/SDA: U3.14 (SDA); also elsewhere on the board
SDO/SA0: U3.1 (SDO/SA0); also elsewhere on the board
VDD: C3.2, C4.1, U3.5 (VDDIO), U3.8 (VDD); also elsewhere on the board

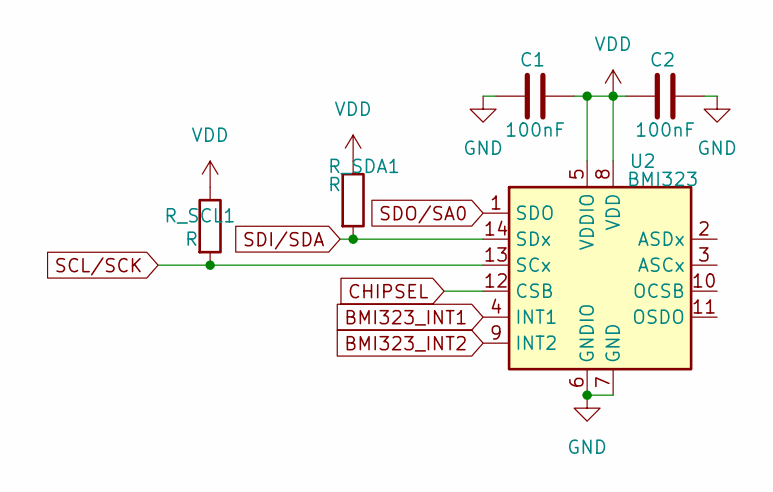
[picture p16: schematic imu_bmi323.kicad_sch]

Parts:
C1, C2: 100nF; C_0402_1005Metric
R_SCL1: R; R_0603_1608Metric
R_SDA1: R; R_0603_1608Metric
U2: BMI323; Bosch_LGA-14_3x2.5mm_P0.5mm

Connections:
BMI323_INT1: U2.4 (INT1); also elsewhere on the board
BMI323_INT2: U2.9 (INT2); also elsewhere on the board
CHIPSEL: U2.12 (CSB); also elsewhere on the board
GND: C1.1, C2.2, U2.6 (GNDIO), U2.7 (GND); also elsewhere on the board
SCL/SCK: R_SCL1.2, U2.13 (SCx); also elsewhere on the board
SDI/SDA: R_SDA1.2, U2.14 (SDx); also elsewhere on the board
SDO/SA0: U2.1 (SDO); also elsewhere on the board
VDD: C1.2, C2.1, R_SCL1.1, R_SDA1.1, U2.5 (VDDIO), U2.8 (VDD); also elsewhere on the board

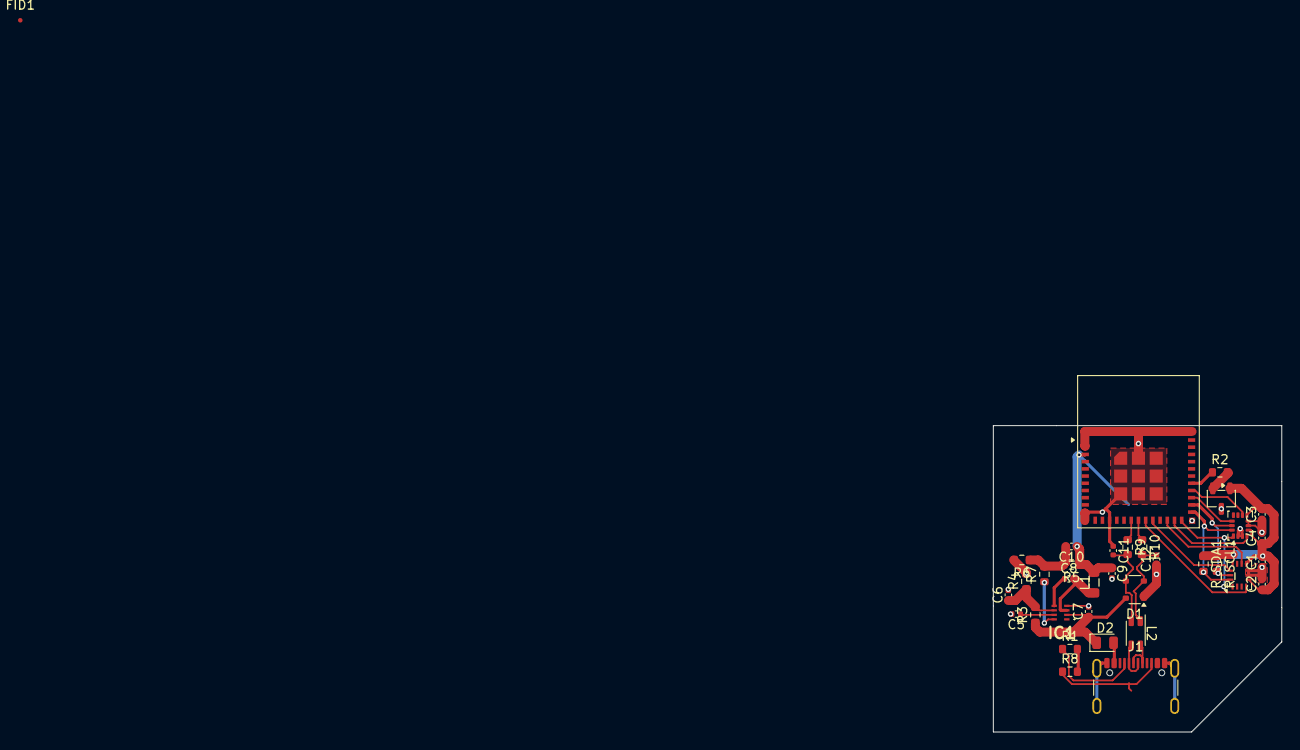
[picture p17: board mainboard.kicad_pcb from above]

Board: 2 copper layers, 32.0 x 34.0 mm, 35 parts (0 on the bottom side), 30 nets.

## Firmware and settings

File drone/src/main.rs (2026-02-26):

#![no_std]
#![no_main]
#![deny(
    clippy::mem_forget,
    reason = "mem::forget is generally not safe to do with esp_hal types, especially those \
    holding buffers for the duration of a data transfer."
)]

extern crate alloc;
use core::iter::zip;

use drone::defmt::defmt_data_to_drone_responses;
use drone::{motors, sensor_fusion};
use embassy_futures::select::{Either, select};
use embassy_sync::{channel, zerocopy_channel};
use embassy_time::{Duration, Instant, Ticker};
use esp_backtrace as _;

use alloc::format;
use defmt::{error, info, warn};
use drone::esp_ikarus::bmi323;
use embassy_executor::Spawner;
use embassy_sync::blocking_mutex::raw::{CriticalSectionRawMutex, NoopRawMutex};
use embassy_sync::channel::{Receiver, Sender};
use esp_hal::clock::CpuClock;
use esp_hal::peripherals::{Peripherals, SW_INTERRUPT, TIMG0, WIFI};
use esp_hal::timer::timg::TimerGroup;

use common_esp::{mpmc_channel, spsc_channel};
use common_messages::{DroneResponse, PingTarget, RemoteRequest, Telemetry};

// This creates a default app-descriptor required by the esp-idf bootloader.
// For more information see: <https://docs.espressif.com/projects/esp-idf/en/stable/esp32/api-reference/system/app_image_format.html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>
esp_bootloader_esp_idf::esp_app_desc!();

// Restart the system on panic
#[unsafe(no_mangle)]
pub fn custom_halt() -> ! {
    esp_hal::system::software_reset()
}

const MOTOR_FRONT_LEFT_IDX: usize = 1;
const MOTOR_FRONT_LEFT_REV: bool = false;

const MOTOR_FRONT_RIGHT_IDX: usize = 2;
const MOTOR_FRONT_RIGHT_REV: bool = true;

const MOTOR_BACK_RIGHT_IDX: usize = 3;
const MOTOR_BACK_RIGHT_REV: bool = false;

const MOTOR_BACK_LEFT_IDX: usize = 0;
const MOTOR_BACK_LEFT_REV: bool = true;

const UNCONFIRMED_ARM_TIME: Duration = Duration::from_millis(500);
const IDLE_THRUST: f32 = 70.0;

#[esp_rtos::main]
async fn main(spawner: Spawner) -> ! {
    let peripherals = init_esp().await;
    init_rtos(peripherals.TIMG0, peripherals.SW_INTERRUPT).await;
    info!("Embassy initialized!");

    // Initialize connection to remote controller
    let (remote_reqests, drone_responses) = {
        let drone = mpmc_channel!(DroneResponse, 64);
        let remote = mpmc_channel!(RemoteRequest, 64);

        spawner.must_spawn(esp_now_communicate(
            peripherals.WIFI,
            drone.receiver(),
            remote.sender(),
        ));
        spawner.must_spawn(defmt_data_to_drone_responses(drone.sender()));

        (remote.receiver(), drone.sender())
    };

    let mut imu_data = {
        info!("IMU init...");

        // Drone:
        let poci = peripherals.GPIO5;
        let imu_cs = peripherals.GPIO23;
        let pico = peripherals.GPIO4;
        let sck = peripherals.GPIO16;
        let imu_int1 = peripherals.GPIO22;
        // // Board:
        // let imu_cs = peripherals.GPIO0;
        // let poci = peripherals.GPIO1;
        // let pico = peripherals.GPIO2;
        // let sck = peripherals.GPIO3;
        // let imu_int1 = peripherals.GPIO14;

        let imu_spi = peripherals.SPI2;
        let imu_dma = peripherals.DMA_CH0;

        embassy_time::Timer::after_millis(500).await;

        let mut imu = bmi323::BMI323::new(imu_spi, sck, pico, poci, imu_dma, imu_cs, imu_int1);
        if let Err(err) = imu.configure().await {
            error!("{}", format!("{err}"));
            panic!("{}", err);
        }

        info!("IMU initialized!");

        let (imu_data_tx, imu_data_rx) = spsc_channel!(bmi323::Sample, 32).split();
        spawner.must_spawn(bmi323::read_imu(imu, imu_data_tx));

        imu_data_rx
    };

    let mut motors = motors::Motors::oneshot125(
        peripherals.RMT,
        peripherals.GPIO19,
        (peripherals.GPIO6, peripherals.GPIO20),
    )
    .await;
    motors.arm_oneshot().await;

    let mut fusion = sensor_fusion::ComplementaryFilterFusion::new(
        0.95, [0.0; 3], [0.0; 3], [25.0; 3], [0.0; 3], [10.0; 3],
    );

    let mut telemetry = {
        let (tx, rx) = spsc_channel!(Telemetry, 1).split();
        spawner.must_spawn(log_send_telementry(rx, drone_responses));
        tx
    };

    let mut inputs = {
        let (tx, rx) = spsc_channel!(Input, 16).split();
        spawner.must_spawn(handle_remote_requests(remote_reqests, drone_responses, tx));
        rx
    };

    let mut thrust = 0.0;
    let mut armed = false;
    let mut motors_saturated = false;

    loop {
        if let Some(input) = inputs.try_receive() {
            match input {
                Input::Armed(true) => {
                    armed = true;
                    info!("armed main");
                }
                Input::Armed(false) => {
                    armed = false;
                    info!("disarmed main");
                }
                Input::Target(new_target) => fusion.set_target(*new_target),
                Input::Thrust(new_thrust) => thrust = *new_thrust,
                Input::Tune { kp, ki, kd } => {
                    for i in 0..3 {
                        fusion.pid[i].k_p = kp[i];
                        fusion.pid[i].k_i = ki[i];
                        // reset sum for integral term
                        fusion.pid[i].sum = 0.0;
                        fusion.pid[i].k_d = kd[i];
                    }
                }
            }
            inputs.receive_done();
        }

        let imu_sample = imu_data.receive().await;
        defmt::debug!(
            "imu: roll={:02}, \tpitch={:02}, \tyaw={:02}, \t\tax={:02}, \tay={:02}, \taz={:02}, \ttime={}",
            imu_sample.gyro[0],
            imu_sample.gyro[1],
            imu_sample.gyro[2],
            imu_sample.accl[0],
            imu_sample.accl[1],
            imu_sample.accl[2],
            imu_sample.time,
        );
        let [roll, pitch, yaw] = fusion.advance(*imu_sample, motors_saturated);
        imu_data.receive_done();

        let motor_throttles = [
            thrust - roll - pitch + yaw,
            thrust + roll - pitch - yaw,
            thrust + roll + pitch + yaw,
            thrust - roll + pitch - yaw,
        ];

        let clamped_throttles = motor_throttles
            // .map(|f| f.clamp(-1000.0, 1000.0));
            .map(|f| f.clamp(IDLE_THRUST, 1000.0));

        motors_saturated =
            zip(motor_throttles, clamped_throttles).any(|(raw, clamped)| raw > clamped);

        let mapped_motor_throttles = map_motor_throttles(clamped_throttles);
        if armed {
            motors.send_throttles(mapped_motor_throttles);
        } else {
            motors.send_throttles([1000; 4]);
        }

        if !armed || thrust < IDLE_THRUST {
            // reset PID integrator when disarmed or low thrust
            fusion.pid.iter_mut().for_each(|pid| pid.sum = 0.0);
        }

        if let Some(msg) = telemetry.try_send() {
            *msg = Telemetry {
                timestamp: Instant::now().as_millis(),
                orientation: fusion.orientation(),
                thrust,
                armed,
                output: [roll, pitch, yaw],
                throttles: mapped_motor_throttles,
            };
            telemetry.send_done();
        };
    }
}

enum Input {
    Thrust(f32),
    Target([f32; 3]),
    Tune {
        kp: [f32; 3],
        ki: [f32; 3],
        kd: [f32; 3],
    },
    Armed(bool),
}

#[embassy_executor::task]
async fn handle_remote_requests(
    remote_requests: channel::Receiver<'static, CriticalSectionRawMutex, RemoteRequest, 64>,
    drone_responses: channel::Sender<'static, CriticalSectionRawMutex, DroneResponse, 64>,
    mut inputs: zerocopy_channel::Sender<'static, NoopRawMutex, Input>,
) -> ! {
    let mut armed = false;
    let mut arm_ticker = Ticker::every(UNCONFIRMED_ARM_TIME);
    let mut thrust = 0.0;

    loop {
        let Either::First(remote_req) = select(remote_requests.receive(), arm_ticker.next()).await
        else {
            if armed {
                warn!("Arm not confirmed in time, disarming...");
                armed = false;
                *inputs.send().await = Input::Armed(false);
                inputs.send_done();
            }

            // Not armed, ignoring
            continue;
        };

        match remote_req {
            RemoteRequest::Ping(target @ PingTarget::Drone, id) => {
                drone_responses.send(DroneResponse::Pong(target, id)).await;
            }
            RemoteRequest::SetArm(true) => {
                if thrust > 10.0 {
                    warn!("drone may not arm when thrust not zero");
                } else {
                    info!("armed");
                    armed = true;
                    arm_ticker.reset();
                    *inputs.send().await = Input::Armed(true);
                    inputs.send_done();
                }

                drone_responses.send(DroneResponse::ArmState(armed)).await;
            }
            RemoteRequest::SetArm(false) => {
                info!("disarmed");
                armed = false;
                *inputs.send().await = Input::Armed(false);
                inputs.send_done();

                drone_responses.send(DroneResponse::ArmState(armed)).await;
            }
            RemoteRequest::ArmConfirm => {
                if armed {
                    arm_ticker.reset();
                } else {
                    warn!("tried to arm confirm unarmed drone");
                }
            }
            RemoteRequest::SetThrust(new_thrust) => {
                thrust = new_thrust;
                *inputs.send().await = Input::Thrust(new_thrust);
                inputs.send_done();
                *inputs.send().await = Input::Thrust(new_thrust);
                inputs.send_done();
            }
            RemoteRequest::SetTarget(target) => {
                *inputs.send().await = Input::Target(target);
                inputs.send_done();
            }
            RemoteRequest::SetTune { kp, ki, kd } => {
                *inputs.send().await = Input::Tune { kp, ki, kd };
                inputs.send_done();
            }
            RemoteRequest::Reset => {
                if armed && thrust > 10.0 {
                    warn!("tried to reset armed and active drone");
                }
                esp_hal::system::software_reset();
            }
            req => warn!("unknown remote request received: {}", req),
        }
    }
}

#[embassy_executor::task]
async fn log_send_telementry(
    mut telemetry: zerocopy_channel::Receiver<'static, NoopRawMutex, Telemetry>,
    drone_responses: channel::Sender<'static, CriticalSectionRawMutex, DroneResponse, 64>,
) -> ! {
    let mut ticker = Ticker::every(Duration::from_millis(250));
    loop {
        ticker.next().await;

        telemetry.clear();
        let received = *telemetry.receive().await;
        drone_responses
            .send(DroneResponse::Telemetry(received))
            .await;
        telemetry.receive_done();
    }
}

fn map_motor_throttles(throttles: [f32; 4]) -> [u16; 4] {
    [
        if MOTOR_FRONT_LEFT_REV {
            -throttles[MOTOR_FRONT_LEFT_IDX]
        } else {
            throttles[MOTOR_FRONT_LEFT_IDX]
        },
        if MOTOR_FRONT_RIGHT_REV {
            -throttles[MOTOR_FRONT_RIGHT_IDX]
        } else {
            throttles[MOTOR_FRONT_RIGHT_IDX]
        },
        if MOTOR_BACK_RIGHT_REV {
            -throttles[MOTOR_BACK_RIGHT_IDX]
        } else {
            throttles[MOTOR_BACK_RIGHT_IDX]
        },
        if MOTOR_BACK_LEFT_REV {
            -throttles[MOTOR_BACK_LEFT_IDX]
        } else {
            throttles[MOTOR_BACK_LEFT_IDX]
        },
    ]
    .map(|t| t + 1000.0)
    .map(|t| t as u16)
}

#[embassy_executor::task]
async fn esp_now_communicate(
    wifi: WIFI<'static>,
    outgoing: Receiver<'static, CriticalSectionRawMutex, DroneResponse, 64>,
    incoming: Sender<'static, CriticalSectionRawMutex, RemoteRequest, 64>,
) {
    common_esp::communicate(wifi, outgoing, incoming).await;
}

async fn init_esp() -> Peripherals {
    let config = esp_hal::Config::default().with_cpu_clock(CpuClock::max());
    let peripherals = esp_hal::init(config);

    esp_alloc::heap_allocator!(#[esp_hal::ram(reclaimed)] size: 65536);

    peripherals
}

async fn init_rtos(timer_group_0: TIMG0<'static>, sw_interrupt: SW_INTERRUPT<'static>) {
    let timg0 = TimerGroup::new(timer_group_0);
    let sw_interrupt = esp_hal::interrupt::software::SoftwareInterruptControl::new(sw_interrupt);
    esp_rtos::start(timg0.timer0, sw_interrupt.software_interrupt0);
}

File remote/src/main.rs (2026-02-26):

use std::time::Duration;

use anyhow::{Result as AnyResult, anyhow};
use bevy::DefaultPlugins;
use bevy::app::{App, AppExit, FixedUpdate, Startup, Update};
use bevy::camera::Camera2d;
use bevy::ecs::message::{MessageReader, MessageWriter};
use bevy::ecs::name::Name;
use bevy::ecs::query::Changed;
use bevy::ecs::resource::Resource;
use bevy::ecs::system::{Commands, IntoSystem, Local, Query, Res, ResMut};
use bevy::input::ButtonState;
use bevy::input::gamepad::{
    Gamepad, GamepadAxis, GamepadAxisChangedEvent, GamepadButton, GamepadConnectionEvent,
};
use bevy::input::keyboard::{KeyCode, KeyboardInput};
use bevy::input_focus::InputDispatchPlugin;
use bevy::input_focus::tab_navigation::TabNavigationPlugin;
use bevy::log::{Level, debug, error, error_once, info, trace, warn};
use bevy::time::Time;
use bevy_egui::EguiPrimaryContextPass;
use common_messages::{DroneResponse, PingId, PingTarget, RemoteRequest};

mod rtt;
use rtt::{
    DroneMessage, DroneTag, ElfResource, LogMessage, RelayTag, RemoteMessage,
    rtt_communication_system,
};

use crate::rtt::{LogSource, log_error_system};
use crate::ui::ui_system;

mod ui;

fn main() -> AnyResult<()> {
    let mut args = std::env::args().skip(1);
    let Some(relay_elf_path) = args.next() else {
        return Err(anyhow!("Expected path to relay elf as first argument"));
    };
    let Some(drone_elf_path) = args.next() else {
        return Err(anyhow!("Expected path to drone elf as second argument"));
    };

    App::new()
        .add_plugins((
            DefaultPlugins,
            InputDispatchPlugin,
            TabNavigationPlugin,
            bevy_egui::EguiPlugin::default(),
        ))
        .insert_resource(KeepArmed(false))
        .insert_resource(ElfResource::<RelayTag>::new(relay_elf_path)?)
        .insert_resource(ElfResource::<DroneTag>::new(drone_elf_path)?)
        .insert_resource(GamepadStatus::default())
        .insert_resource(PingStatus::default())
        .add_message::<RemoteMessage>()
        .add_message::<DroneMessage>()
        .add_message::<LogMessage>()
        .add_systems(Startup, setup_camera_system)
        .add_systems(EguiPrimaryContextPass, ui_system)
        .add_systems(Update, (keyboard_input_system, gamepad_input_system))
        .add_systems(
            FixedUpdate,
            (
                rtt_communication_system.pipe(log_error_system),
                keep_armed_system,
                ping_pong_system,
            ),
        )
        // .add_systems(FixedPostUpdate, log_logs)
        .run();

    Ok(())
}

fn setup_camera_system(mut commands: Commands) {
    commands.spawn(Camera2d);
}

#[allow(dead_code)]
fn log_logs(mut logs: MessageReader<LogMessage>) {
    for LogMessage(source, level, message) in logs.read() {
        if *source == LogSource::Relay {
            continue;
        }
        match (*level, *source) {
            (Level::ERROR, LogSource::Drone) => error!(target: "drone", "{message}"),
            (Level::WARN, LogSource::Drone) => warn!(target: "drone", "{message}"),
            (Level::INFO, LogSource::Drone) => info!(target: "drone", "{message}"),
            (Level::DEBUG, LogSource::Drone) => debug!(target: "drone", "{message}"),
            (Level::TRACE, LogSource::Drone) => trace!(target: "drone", "{message}"),
            (Level::ERROR, LogSource::Relay) => error!(target: "relay", "{message}"),
            (Level::WARN, LogSource::Relay) => warn!(target: "relay", "{message}"),
            (Level::INFO, LogSource::Relay) => info!(target: "relay", "{message}"),
            (Level::DEBUG, LogSource::Relay) => debug!(target: "relay", "{message}"),
            (Level::TRACE, LogSource::Relay) => trace!(target: "relay", "{message}"),
        };
    }
}

#[derive(Resource)]
struct KeepArmed(bool);

fn keep_armed_system(
    keep_armed: Res<KeepArmed>,
    time: Res<Time>,
    mut time_last_sent: Local<Duration>,
    mut remote_msgs: MessageWriter<RemoteMessage>,
) {
    let current = time.elapsed();
    let time_has_elapsed = (current - *time_last_sent) >= Duration::from_millis(100);
    if keep_armed.0 && time_has_elapsed {
        *time_last_sent = current;
        remote_msgs.write(RemoteMessage(RemoteRequest::ArmConfirm));
    }
}

#[derive(Resource, Default)]
struct PingStatus {
    roundtrip_relay: Option<Duration>,
    pings_relay: Vec<(PingId, Duration)>,
    roundtrip_drone: Option<Duration>,
    pings_drone: Vec<(PingId, Duration)>,
    next_id: PingId,
}

fn ping_pong_system(
    mut ping_status: ResMut<PingStatus>,
    time: Res<Time>,
    mut time_last_sent: Local<Duration>,
    mut remote_msgs: MessageWriter<RemoteMessage>,
    mut drone_msgs: MessageReader<DroneMessage>,
) {
    let current = time.elapsed();

    for DroneMessage(res) in drone_msgs.read() {
        let DroneResponse::Pong(pong_src, pong_id) = res else {
            continue;
        };

        let pings = match pong_src {
            PingTarget::Relay => &mut ping_status.pings_relay,
            PingTarget::Drone => &mut ping_status.pings_drone,
        };

        let Some((_, sent_time)) = pings.iter().find(|(id, _)| id == pong_id).cloned() else {
            warn!("Received unkown Pong({pong_src:?}, {pong_id})");
            continue;
        };
        pings.retain(|(id, _)| id != pong_id);

        match pong_src {
            PingTarget::Relay => ping_status.roundtrip_relay = Some(current - sent_time),
            PingTarget::Drone => ping_status.roundtrip_drone = Some(current - sent_time),
        };
    }

    if (current - *time_last_sent) >= Duration::from_millis(500) {
        *time_last_sent = current;
        let ping_id = ping_status.next_id;

        remote_msgs.write_batch([
            RemoteMessage(RemoteRequest::Ping(PingTarget::Relay, ping_id)),
            RemoteMessage(RemoteRequest::Ping(PingTarget::Drone, ping_id)),
        ]);
        ping_status.pings_relay.push((ping_id, current));
        ping_status.pings_drone.push((ping_id, current));

        ping_status.next_id = ping_id.wrapping_add(1);
    }

    if ping_status.pings_relay.len() > 2 {
        ping_status.roundtrip_relay = None;
        ping_status.pings_relay.clear();
    }
    if ping_status.pings_drone.len() > 2 {
        ping_status.roundtrip_drone = None;
        ping_status.pings_drone.clear();
    }
}

fn keyboard_input_system(
    mut inputs: MessageReader<KeyboardInput>,
    mut exit: MessageWriter<AppExit>,
) {
    for input in inputs.read().filter(|i| i.state == ButtonState::Released) {
        match input.key_code {
            KeyCode::Escape | KeyCode::KeyQ => {
                exit.write(AppExit::Success);
            }
            _ => {}
        };
    }
}

#[derive(Resource, Default)]
struct GamepadStatus {
    connected: bool,
    had_input: bool,
}
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

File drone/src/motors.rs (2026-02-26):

use core::marker::PhantomData;

use defmt::error;
use embassy_time::{Duration, Instant};
use esp_hal::{
    Blocking,
    gpio::{Level, Output, OutputConfig, OutputPin, interconnect::PeripheralOutput},
    peripherals::RMT,
    rmt::{Channel, PulseCode, Rmt, Tx, TxChannelConfig, TxChannelCreator},
    time::Rate,
};

pub trait Protocol {
    const RATE: Rate;
    const CLK_DIV: u8;

    /// transforms a throttle from 0..=2000 into protocol range
    fn throttle_transform(throttle: u16) -> u16;
    fn encode_pulse(value: u16) -> impl AsRef<[PulseCode]>;
}

pub trait OneShot: Protocol {
    fn throttle_transform(throttle: u16) -> u16 {
        (throttle / 2).min(1000) + 1000
    }

    fn encode_oneshot_pulse(value: u16) -> impl AsRef<[PulseCode]> {
        // Low length of 0 is ok because we multiplex that line.
        // For the time we talk to the other esc the line is low anyway,
        // so we don't have to wait for it here.
        [
            PulseCode::new(Level::High, value, Level::Low, 0),
            PulseCode::end_marker(),
        ]
    }
}

pub struct OneShot125;
impl OneShot for OneShot125 {}
impl Protocol for OneShot125 {
    // 8 MHz -> 0.125µs
    // throttle = 1000 => pulse of 125µs which is 0 for OneShot125
    // throttle = 2000 => pulse of 250µs which is full throttle for OneShot125
    const RATE: Rate = Rate::from_mhz(8);
    const CLK_DIV: u8 = 1;

    fn throttle_transform(throttle: u16) -> u16 {
        <Self as OneShot>::throttle_transform(throttle)
    }

    fn encode_pulse(value: u16) -> impl AsRef<[PulseCode]> {
        Self::encode_oneshot_pulse(value)
    }
}

pub struct OneShot42;
impl OneShot for OneShot42 {}
impl Protocol for OneShot42 {
    // 24 MHz -> ~0.042µs
    // throttle = 1000 => pulse of 42µs which is 0 for OneShot42
    // throttle = 2000 => pulse of 48µs which is full throttle for OneShot42
    const RATE: Rate = Rate::from_mhz(24);
    const CLK_DIV: u8 = 1;

    fn throttle_transform(throttle: u16) -> u16 {
        <Self as OneShot>::throttle_transform(throttle)
    }

    fn encode_pulse(value: u16) -> impl AsRef<[PulseCode]> {
        Self::encode_oneshot_pulse(value)
    }
}

pub struct Motors<Protocol> {
    data: Channel<'static, Blocking, Tx>,
    mux_slct: [Output<'static>; 2],
    protocol: PhantomData<Protocol>,
}

impl<Proto: Protocol> Motors<Proto> {
    pub async fn new(
        rmt: RMT<'static>,
        data_pin: impl PeripheralOutput<'static>,
        mux_slct: (impl OutputPin + 'static, impl OutputPin + 'static),
    ) -> Self {
        let rmt = Rmt::new(rmt, Proto::RATE).expect("rmt setup");
        let channel = rmt
            .channel0
            .configure_tx(
                data_pin,
                TxChannelConfig::default()
                    .with_clk_divider(Proto::CLK_DIV)
                    .with_idle_output_level(Level::Low)
                    .with_idle_output(true)
                    .with_carrier_modulation(false)
                    .with_memsize(1),
            )
            .expect("rmt tx channel 0");

        let mux_slct0 = Output::new(mux_slct.1, Level::Low, OutputConfig::default());
        let mux_slct1 = Output::new(mux_slct.0, Level::Low, OutputConfig::default());

        Self {
            data: channel,
            mux_slct: [mux_slct0, mux_slct1],
            protocol: Default::default(),
        }
    }

    fn send_esc_value(&mut self, value: u16) {
        let pulse = Proto::encode_pulse(value);

        let channel = self.data.reborrow();

        if let Err(e) = channel
            .transmit(pulse.as_ref())
            .map(|tx| tx.wait().map_err(|(e, _)| e))
        {
            error!("unable to transmit rmt pulse: {:?}", e)
        }
    }

    pub fn send_esc_values(&mut self, values: [u16; 4]) {
        critical_section::with(|_cs| {
            self.mux_slct[0].set_low();
            self.mux_slct[1].set_low();
            self.send_esc_value(values[0]);

            self.mux_slct[0].set_low();
            self.mux_slct[1].set_high();
            self.send_esc_value(values[1]);

            self.mux_slct[0].set_high();
            self.mux_slct[1].set_low();
            self.send_esc_value(values[2]);

            self.mux_slct[1].set_high();
            self.mux_slct[1].set_high();
            self.send_esc_value(values[3]);
        })
    }

    pub fn send_throttles(&mut self, throttles: [u16; 4]) {
        self.send_esc_values(throttles.map(Proto::throttle_transform))
    }
}

impl<Proto: OneShot> Motors<Proto> {
    pub async fn arm_oneshot(&mut self) {
        let end = Instant::now().saturating_add(Duration::from_secs(3));
        while Instant::now() <= end {
            self.send_throttles([1000; 4]);
        }
    }
}

impl Motors<OneShot125> {
    pub async fn oneshot125(
        rmt: RMT<'static>,
        data_pin: impl PeripheralOutput<'static>,
        mux_slct: (impl OutputPin + 'static, impl OutputPin + 'static),
    ) -> Self {
        Self::new(rmt, data_pin, mux_slct).await
    }
}

impl Motors<OneShot42> {
    pub async fn oneshot42(
        rmt: RMT<'static>,
        data_pin: impl PeripheralOutput<'static>,
        mux_slct: (impl OutputPin + 'static, impl OutputPin + 'static),
    ) -> Self {
        Self::new(rmt, data_pin, mux_slct).await
    }
}

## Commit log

2025-11-04 very basic imu test setup
2025-11-16 mainboard rev0
    [mainboard.kicad_pcb, mainboard.kicad_sch]
2025-11-16 mainboard rev1
    [imu_bmi323.kicad_sch, imu_lsm6ds3.kicad_sch]
2025-11-16 mainboard edits
    [imu_bmi323.kicad_sch, imu_lsm6ds3.kicad_sch, mainboard.kicad_pcb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]
2025-12-04 feat(imu): gather IMU readings via SPI
2025-12-04 feat(imu): raw data visualization
2025-12-04 feat(imu): implement bmi323
2026-01-14 feat(esp_now): remove ’static in even more places
2026-01-16 feat(merge_everything): fix all build errors for drone
    [bmi323.rs, lsm6ds3.rs, main.rs]
2026-01-23 feat(merge_everything): integrate imu
2026-01-23 feat(merge_everything): clean up and fix lints
    [main.rs]
2026-02-10 feat(logging): use probe-rs
2026-02-12 feat(remote): decode defmt in separate thread
2026-02-18 feat(message): en/decode message frames
2026-02-20 feat(sensor_fusion): implement complementary filter and pid controller for roll, pitch and yaw
2026-02-20 feat(sensor_fusion): fix filter
2026-02-20 feat(sensor_fusion): control loops are now controlling
2026-02-20 feat(sensor_fusion): fix motor mapping
    [main.rs]
2026-02-20 fix(sensor_fusion):    
    [main.rs]
2026-02-24 fix(arm_confirm): refactor drone control loop
    [main.rs]
2026-02-24 feat(arm_confirm): send arm confirm continually from terminal
2026-02-24 fix(arm_confirm): properly receive inputs
    [main.rs]
2026-02-24 fix(imu_shenanigans): fix rust analyzer
    [main.rs]
2026-02-24 fix(imu_shenanigans): fix spi transactions
    [bmi323.rs, lsm6ds3.rs, main.rs]
2026-02-25 fix(pid_targets): set yaw as rotation speed target
2026-02-25 fix(motors): set lower motor bound when armed
    [main.rs]
2026-02-25 feat(gamepad): add arming buttons mapping
2026-02-26 feat(gui): send pings every 500ms, add reset button
2026-02-26 fix(gui): fix drone logs
    [main.rs]
2026-02-26 feat(gui): track gamepad status
2026-02-26 fix(pid): prevent integrator windup
    [main.rs]
2026-02-26 fix(mototrs): wrap rmt transmit and multiplex switching in critical section
    [main.rs, motors.rs]
